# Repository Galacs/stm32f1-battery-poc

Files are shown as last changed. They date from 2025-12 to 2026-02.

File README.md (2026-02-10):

# STM32F1 Battery POC

STM32F1 based pcb to test 3s Li-ion cells protection with 3 phases brushless and steppers driver interfaces.

## IC List

- STM32F103C8T (Main MCU)
- QRE1113 (reflectance sensor)
- HT753-1 (3v3 LDO)
- LM78M (5v LDO)
- DRV8311 (BLDC driver)
- DRV8424 (Stepper driver)
- BQ77905 (3S battery protection)
- SN65HVD (CAN transceiver)

## Top preview




## Preview 3d render




## Pictures



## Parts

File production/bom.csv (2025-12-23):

Designator | Footprint | Quantity | Value | LCSC Part #
C1, C22, C23, C24, C31, C32, C34, C35, C41 | 0402 | 9 | 1u | C52923
C10, C15 | 0402 | 2 | 22n | C1532
C11, C12, C16, C18, C21, C26, C27, C28, C29, C3, C30, C33, C37, C38, C4, C40, C5, C6, C7 | 0402 | 19 | 0u1 | C307331
C13, C14 | 0603 | 2 | 20p | C1648
C17, C25, C36 | 0402 | 3 | 10n | C15195
C19 | 0603 | 1 | 0u47 | C1623
C2, C39, C43, C8, C9 | 0805 | 5 | 10u | C440198
C20, C42 | CP_Elec_6.3x7.7 | 2 | 100u | C165974
D1 | 0805 | 1 | YELLOW | C2296
D2 | 0603 | 1 | WHITE | C2290
D3 | 0805 | 1 | GREEN | C2297
D4 | 0603 | 1 | RED | C2286
D5 | D_SMB | 1 | D_TVS | C2925441
D6 | D_SOD-323 | 1 | 100 | C2128
D7 | D_SOD-123 | 1 | 16 | C19077429
FB1, FB2 | 0805 | 2 | 600Ω@100M | C1015
Q1, Q2 | Vishay_PowerPAK_1212-8_Single | 2 | Q_NMOS | C111309
R1, R32, R33, R6 | 0402 | 4 | 5k1 | C25905
R10, R11, R12 | 0603 | 3 | 47 | C23182
R13, R21 | 0603 | 2 | 330k | C23137
R14, R25, R28 | 0402 | 3 | 100 | C25076
R15, R16, R17, R18, R2, R29, R31 | 0402 | 7 | 10k | C25744
R19 | 0603 | 1 | 560 | C23204
R20, R22, R23, R24, R26 | 0402 | 5 | 1k | C11702
R27 | 1206 | 1 | 10m/1W | C105362
R3, R4, R5 | 0603 | 3 | 6k8 | C23212
R30, R35 | 0402 | 2 | 1M | C26083
R34 | 0603 | 1 | 3M | C23156
R36 | 0603 | 1 | 470k | C23178
R37, R38, R39 | 0402 | 3 | 47k | C25792
R7, R9 | 0603 | 2 | 20k | C4184
R8 | 1206 | 1 | 120 | C17909
SW1, SW2, SW3 | SW_SPST_TS-1088-xR020 | 3 | SW_Push | C720477
U1 | TO-252-2 | 1 | LM78M05 | C5145267
U10 | Texas_RRW0024A_WQFN-24-1EP_2x2mm_P0.4mmThermalVias | 1 | DRV8311H | C5218862
U2 | SOT-89-3 | 1 | HT753-1 | C14289
U3 | SOIC-8_3.9x4.9mm_P1.27mm | 1 | SN65HVD230 | C12084
U4, U5, U6 | OnSemi_CASE100CY | 3 | QRE1113GR | C232862
U7 | Texas_RGE0024B_VQFN-24-1EP_4x4mm_P0.5mm_EP2.5x2.5mm_ThermalVias | 1 | DRV8424RGER | C1518725
U8 | LQFP-48_7x7mm_P0.5mm | 1 | STM32F103C8Tx | C8734
U9 | TSSOP-20_4.4x6.5mm_P0.65mm | 1 | BQ77905 | C2866527
Y1 | Crystal_SMD_5032-2Pin_5.0x3.2mm | 1 | 8M | C115962

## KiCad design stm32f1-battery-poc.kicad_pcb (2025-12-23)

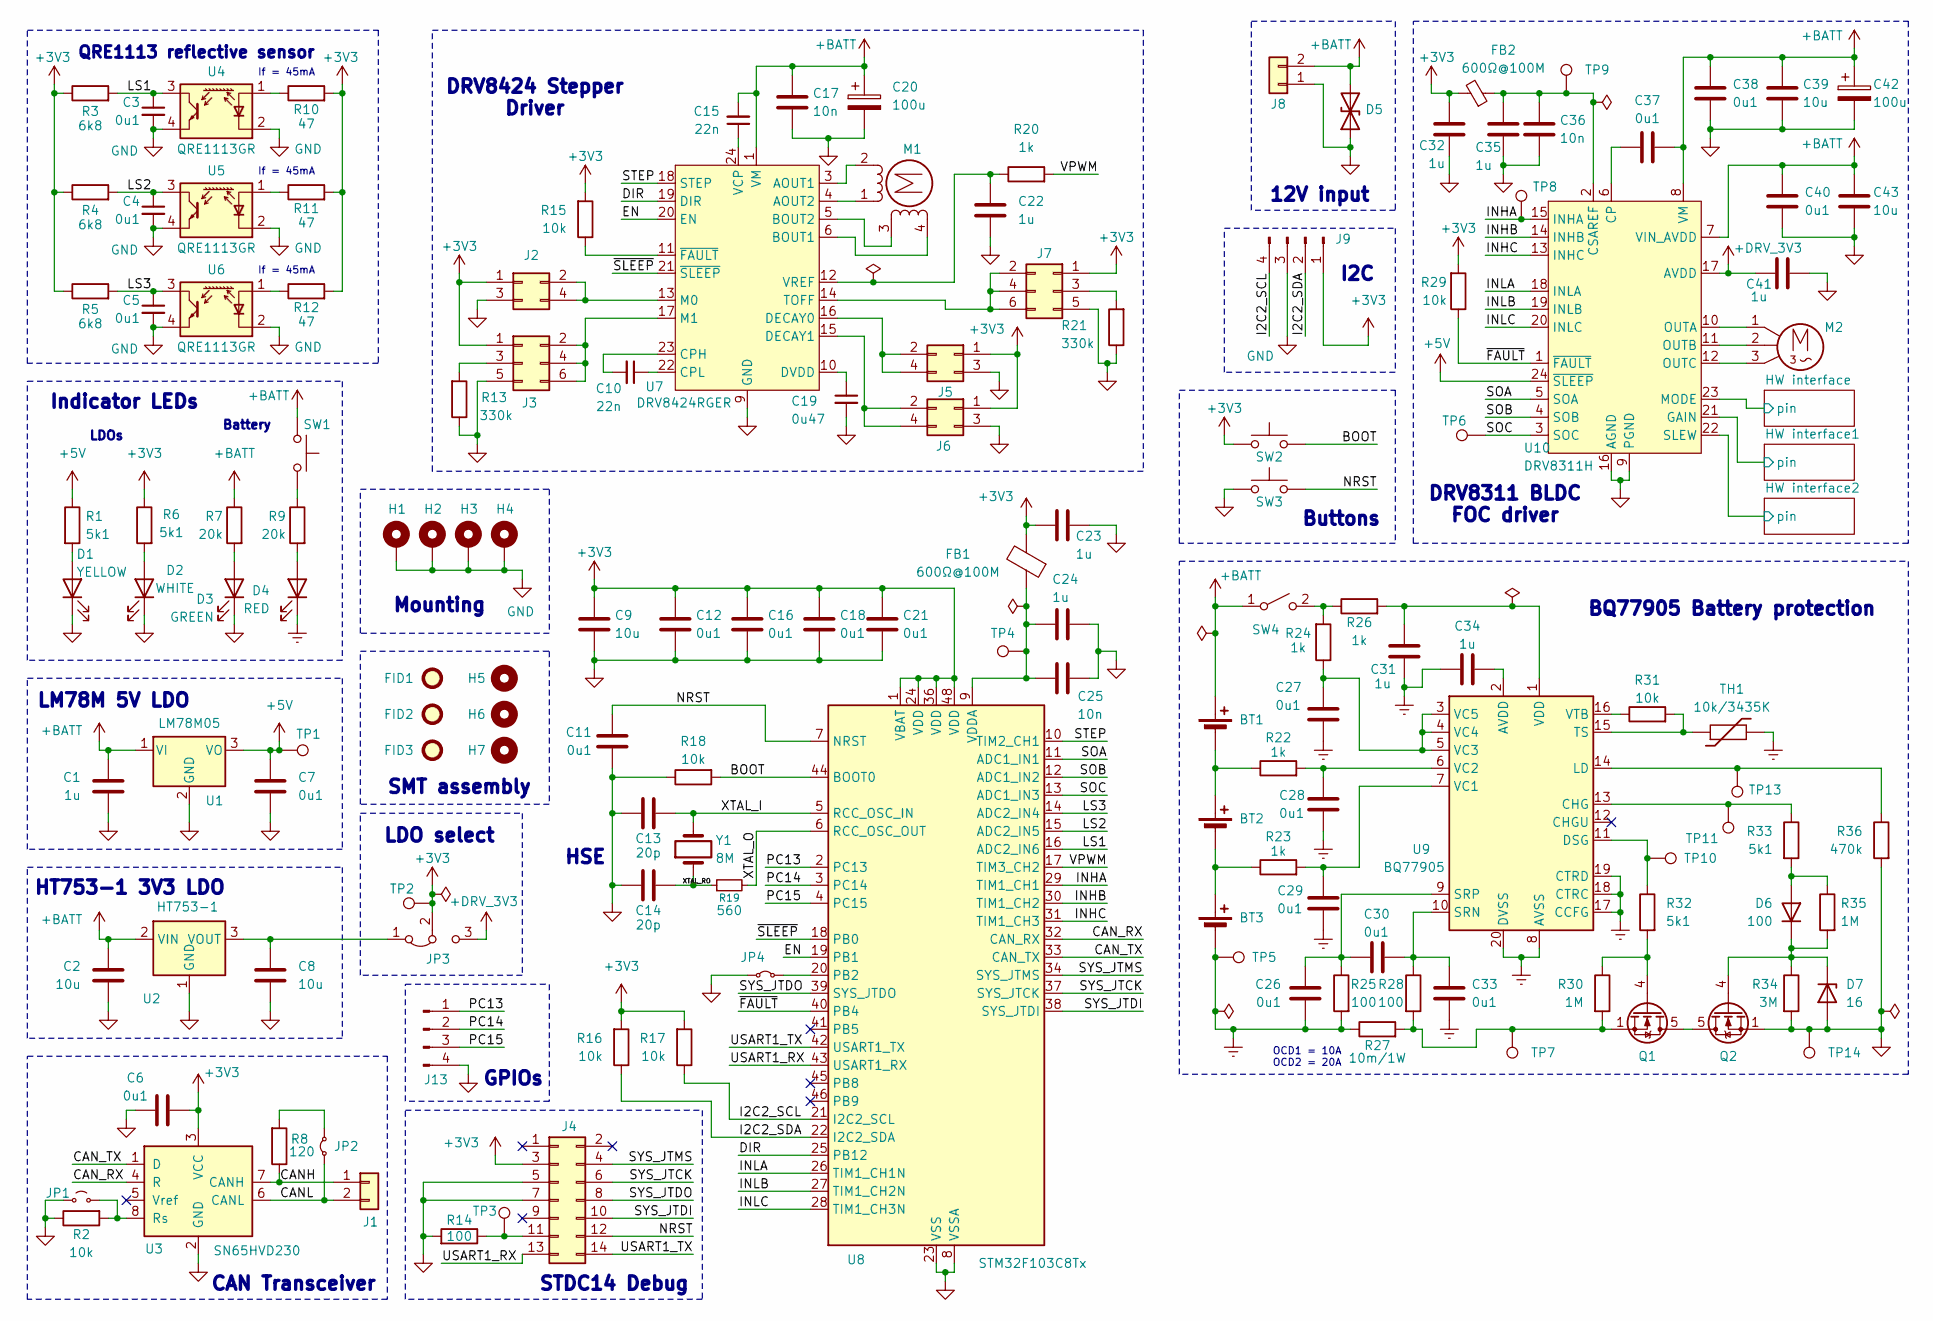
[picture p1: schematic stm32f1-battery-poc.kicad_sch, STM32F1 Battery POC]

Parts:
BT1, BT2, BT3: Battery_Cell; BatteryHolder_MYOUNG_BH-18650-B1BA002
C1, C22, C23, C24, C31, C32, C34, C35, C41: 1u; C_0402_1005Metric; Manufacturer Part Number CL05A105KA5NQNC; JLCPCB Part # C52923
C2, C8, C9, C39, C43: 10u; C_0805_2012Metric; Manufacturer Part Number GRM21BR61H106KE43L; JLCPCB Part # C440198
C3, C4, C5, C6, C7, C11, C12, C16, C18, C21, C26, C27, C28, C29, C30, C33, C37, C38, C40: 0u1; C_0402_1005Metric; Manufacturer Part Number CL05B104KB54PNC; JLCPCB Part # C307331
C10, C15: 22n; C_0402_1005Metric; Manufacturer Part Number 0402B223K500NT; JLCPCB Part # C1532
C13, C14: 20p; C_0603_1608Metric; Manufacturer Part Number CL10C200JB8NNNC; JLCPCB Part # C1648
C17, C25, C36: 10n; C_0402_1005Metric; Manufacturer Part Number CL05B103KB5NNNC; JLCPCB Part # C15195
C19: 0u47; C_0603_1608Metric; Manufacturer Part Number CL10B474KA8NNNC; JLCPCB Part # C1623
C20, C42: 100u; CP_Elec_6.3x7.7; Manufacturer Part Number EEEFTH101XAP; JLCPCB Part # C165974
D1: YELLOW; LED_0805_2012Metric; Manufacturer Part Number KT-0805Y; JLCPCB Part # C2296
D2: WHITE; LED_0603_1608Metric; Manufacturer Part Number KT-0603W; JLCPCB Part # C2290
D3: GREEN; LED_0805_2012Metric; Manufacturer Part Number KT-0805G; JLCPCB Part # C2297
D4: RED; LED_0603_1608Metric; Manufacturer Part Number KT-0603R; JLCPCB Part # C2286
D5: D_TVS; D_SMB; Manufacturer Part Number SMBJ30CA; JLCPCB Part # C2925441
D6: 100; D_SOD-323; Manufacturer Part Number 1N4148WS; JLCPCB Part # C2128
D7: 16; D_SOD-123; Manufacturer Part Number MMSZ5246B; JLCPCB Part # C19077429
FB1, FB2: 600Ω@100M; L_0805_2012Metric; Manufacturer Part Number GZ2012D101TF; JLCPCB Part # C1015
FID1, FID2, FID3: Fiducial; Fiducial_1mm_Mask2mm
H1, H2, H3, H4: MountingHole_Pad; MountingHole_2.2mm_M2_Pad_Via
H5, H6, H7: MountingHole; ToolingHole_1.152mm
J1: Conn_01x02; PinHeader_1x02_P2.54mm_Vertical
J2, J5, J6: Conn_02x02_Odd_Even; PinHeader_2x02_P1.27mm_Vertical_SMD
J3, J7: Conn_02x03_Odd_Even; PinHeader_2x03_P1.27mm_Vertical_SMD
J4: Conn_02x07_Odd_Even; PinHeader_2x07_P1.27mm_Vertical
J8: Conn_01x02; TerminalBlock_Phoenix_MKDS-1,5-2-5.08_1x02_P5.08mm_Horizont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
J9, J13: Conn_01x04_Pin; PinHeader_1x04_P2.54mm_Vertical
JP1: Jumper_2_Small_Open; PinHeader_2x01_P1.27mm_Vertical_SMD
JP2, JP4: Jumper_2_Small_Bridged; PinHeader_2x01_P1.27mm_Vertical_SMD
JP3: Jumper_3_Bridged12; PinHeader_1x03_P1.27mm_Vertical_SMD_Pin1Left
M1: Stepper_Motor_bipolar; JST_XH_S6B-XH-A_Stepper_1x06_P2.50mm_Horizontal
M2: Motor_3_Phases; PinHeader_1x03_P2.54mm_Vertical
Q1, Q2: Q_NMOS; Vishay_PowerPAK_1212-8_Single; Manufacturer Part Number SIS412DN-T1-GE3; JLCPCB Part # C111309
R1, R6, R32, R33: 5k1; R_0402_1005Metric; Manufacturer Part Number 0402WGF5101TCE; JLCPCB Part # C25905
R2, R15, R16, R17, R18, R29, R31: 10k; R_0402_1005Metric; Manufacturer Part Number 0402WGF1002TCE; JLCPCB Part # C25744
R3, R4, R5: 6k8; R_0603_1608Metric; Manufacturer Part Number 0603WAF6801T5E; JLCPCB Part # C23212
R7, R9: 20k; R_0603_1608Metric; Manufacturer Part Number 0603WAF2002T5E; JLCPCB Part # C4184
R8: 120; R_1206_3216Metric; Manufacturer Part Number 1206W4F1200T5E; JLCPCB Part # C17909
R10, R11, R12: 47; R_0603_1608Metric; Manufacturer Part Number 0603WAF470JT5E; JLCPCB Part # C23182
R13, R21: 330k; R_0603_1608Metric; Manufacturer Part Number 0603WAF3303T5E; JLCPCB Part # C23137
R14, R25, R28: 100; R_0402_1005Metric; Manufacturer Part Number 0402WGF1000TCE; JLCPCB Part # C25076
R19: 560; R_0603_1608Metric; Manufacturer Part Number 0603WAF5600T5E; JLCPCB Part # C23204
R20, R22, R23, R24, R26: 1k; R_0402_1005Metric; Manufacturer Part Number 0402WGF1001TCE; JLCPCB Part # C11702
R27: 10m/1W; R_1206_3216Metric; Manufacturer Part Number FMF06FTHR010-LH; JLCPCB Part # C105362
R30, R35: 1M; R_0402_1005Metric; Manufacturer Part Number 0402WGF1004TCE; JLCPCB Part # C26083
R34: 3M; R_0603_1608Metric; Manufacturer Part Number 0603WAF3004T5E; JLCPCB Part # C23156
R36: 470k; R_0603_1608Metric; Manufacturer Part Number 0603WAF4703T5E; JLCPCB Part # C23178
SW1, SW2, SW3: SW_Push; SW_SPST_TS-1088-xR020; Manufacturer Part Number TS-1088-AR02016; JLCPCB Part # C720477
SW4: SW_SPST; PinHeader_1x02_P2.54mm_Vertical
TH1: 10k/3435K; PinSocket_1x02_P2.54mm_Vertical
TP1, TP2, TP3, TP4, TP5, TP6, TP7, TP8, TP9, TP10, TP11, TP13, TP14: TestPoint; TestPoint_Pad_D2.0mm
U1: LM78M05; TO-252-2; Manufacturer Part Number LM78M05ACKTPRG; JLCPCB Part # C5145267
U2: HT753-1; SOT-89-3; Manufacturer Part Number HT7533-1; JLCPCB Part # C14289
U3: SN65HVD230; SOIC-8_3.9x4.9mm_P1.27mm; Manufacturer Part Number SN65HVD230DR; JLCPCB Part # C12084
U4, U5, U6: QRE1113GR; OnSemi_CASE100CY; Manufacturer Part Number QRE1113GR; JLCPCB Part # C232862
U7: DRV8424RGER; Texas_RGE0024B_VQFN-24-1EP_4x4mm_P0.5mm_EP2.5x2.5mm_Thermal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; Manufacturer Part Number DRV8424RGER; JLCPCB Part # C1518725
U8: STM32F103C8Tx; LQFP-48_7x7mm_P0.5mm; Manufacturer Part Number STM32F103C8T6; JLCPCB Part # C8734
U9: BQ77905; TSSOP-20_4.4x6.5mm_P0.65mm; Manufacturer Part Number BQ7790509PWR; JLCPCB Part # C2866527
U10: DRV8311H; Texas_RRW0024A_WQFN-24-1EP_2x2mm_P0.4mmThermalVias; Manufacturer Part Number DRV8311HRRWR; JLCPCB Part # C5218862
Y1: 8M; Crystal_SMD_5032-2Pin_5.0x3.2mm; Manufacturer Part Number X50328MSB2GI; JLCPCB Part # C115962

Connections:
+3V3: C6.1, C9.1, C12.1, C16.1, C18.1, C21.1, C23.1, C32.1, FB1.2, FB2.2, J2.1, J3.1, J4.3, J5.1, J6.1, J7.1, J9.1, JP3.2 (C), R3.1, R4.1, R5.1, R6.1, R10.2, R11.2, R12.2, R15.2, R16.2, R17.2, R29.2, SW2.1, TP2.1, U3.3 (VCC), U8.1 (VBAT), U8.24 (VDD), U8.36 (VDD), U8.48 (VDD); also elsewhere on the board
+5V: C7.1, R1.1, TP1.1, U1.3 (VO), U10.24 (~SLEEP)
+BATT: BT1.1 (+), C1.1, C2.1, C15.2, C17.1, C20.1, C37.2, C38.2, C39.2, C40.2, C42.1, C43.2, D5.2 (A2), J8.2, R7.1, SW1.2, SW4.1 (A), U1.1 (VI), U2.2 (VIN), U7.1 (VM), U7.8 (VM), U10.7 (VIN_AVDD), U10.8 (VM)
+DRV_3V3: C41.1, JP3.3 (B), U10.17 (AVDD)
/BOOT: R18.2, SW2.2, U8.44 (BOOT0)
/CANH: J1.1, R8.1, U3.7 (CANH)
/CANL: J1.2, JP2.1 (A), U3.6 (CANL)
/CAN_RX: U3.4 (R), U8.32 (CAN_RX)
/CAN_TX: U3.1 (D), U8.33 (CAN_TX)
/DIR: U7.19 (DIR), U8.25 (PB12)
/EN: U7.20 (EN), U8.19 (PB1)
/HW interface1/pin: U10.21 (GAIN); also elsewhere on the board
/HW interface2/pin: U10.22 (SLEW); also elsewhere on the board
/HW interface/pin: U10.23 (MODE); also elsewhere on the board
/I2C2_SCL: J9.4, R17.1, U8.21 (I2C2_SCL)
/I2C2_SDA: J9.2, R16.1, U8.22 (I2C2_SDA)
/INHA: TP8.1, U8.29 (TIM1_CH1), U10.15 (INHA)
/INHB: U8.30 (TIM1_CH2), U10.14 (INHB)
/INHC: U8.31 (TIM1_CH3), U10.13 (INHC)
/INLA: U8.26 (TIM1_CH1N), U10.18 (INLA)
/INLB: U8.27 (TIM1_CH2N), U10.19 (INLB)
/INLC: U8.28 (TIM1_CH3N), U10.20 (INLC)
/LS1: C3.1, R3.2, U4.3, U8.16 (ADC2_IN6)
/LS2: C4.1, R4.2, U5.3, U8.15 (ADC2_IN5)
/LS3: C5.1, R5.2, U6.3, U8.14 (ADC2_IN4)
/NRST: C11.1, J4.12, SW3.2, U8.7 (NRST)
/PC13: J13.1, U8.2 (PC13)
/PC14: J13.2, U8.3 (PC14)
/PC15: J13.3, U8.4 (PC15)
/SOA: U8.11 (ADC1_IN1), U10.5 (SOA)
/SOB: U8.12 (ADC1_IN2), U10.4 (SOB)
/SOC: TP6.1, U8.13 (ADC1_IN3), U10.3 (SOC)
/STEP: U7.18 (STEP), U8.10 (TIM2_CH1)
/SYS_JTCK: J4.6, U8.37 (SYS_JTCK)
/SYS_JTDI: J4.10, U8.38 (SYS_JTDI)
/SYS_JTDO: J4.8, U8.39 (SYS_JTDO)
/SYS_JTMS: J4.4, U8.34 (SYS_JTMS)
/USART1_RX: J4.13, U8.43 (USART1_RX)
/USART1_TX: J4.14, U8.42 (USART1_TX)
/VPWM: R20.2, U8.17 (TIM3_CH2)
/XTAL_I: C13.1, U8.5 (RCC_OSC_IN), Y1.2
/XTAL_O: R19.2, U8.6 (RCC_OSC_OUT)
/XTAL_RO: C14.1, R19.1, Y1.1
/~FAULT: R29.1, U8.40 (PB4), U10.1 (~FAULT)
/~SLEEP: U7.21 (~SLEEP), U8.18 (PB0)
BGND: BT3.2 (-), C26.2, C27.2, C28.2, C29.2, C31.1, C33.2, C34.2, D4.1 (K), R25.2, R27.1, TH1.2, TP5.1, U9.8 (AVSS), U9.17 (CCFG), U9.18 (CTRC), U9.19 (CTRD), U9.20 (DVSS)
GND: C1.2, C2.2, C3.2, C4.2, C5.2, C6.2, C7.2, C8.2, C9.2, C11.2, C12.2, C13.2, C14.2, C16.2, C17.2, C18.2, C19.2, C20.2, C21.2, C22.2, C23.2, C24.2, C25.2, C32.2, C35.2, C36.2, C38.1, C39.1, C40.1, C41.2, C42.2, C43.1, D1.1 (K), D2.1 (K), D3.1 (K), D5.1 (A1), D7.2 (A), H1.1, H2.1, H3.1, H4.1, J2.3, J3.5, J4.5, J4.7, J5.3, J6.3, J7.5, J8.1, J9.3, J13.4, JP1.1 (A), JP4.1 (A), Q2.1 (S), Q2.2 (S), Q2.3 (S), R2.1, R13.1, R14.2, R18.1, R21.1, R34.2, R36.2, SW3.1, TP14.1, U1.2 (GND), U2.1 (GND), U3.2 (GND), U4.2 (K), U4.4, U5.2 (K), U5.4, U6.2 (K), U6.4, U7.2 (PGND), U7.7 (PGND), U7.9 (GND), U7.25 (GND), U8.8 (VSSA), U8.23 (VSS), U8.35 (VSS), U8.47 (VSS), U10.9 (PGND), U10.16 (AGND), U10.25 (EPAD); also elsewhere on the board
unnamed: BT1.2 (-), BT2.1 (+), R22.1
unnamed: BT2.2 (-), BT3.1 (+), R23.1
unnamed: D1.2 (A), R1.2
unnamed: D2.2 (A), R6.2
unnamed: D3.2 (A), R7.2
unnamed: D4.2 (A), R9.2
unnamed: D6.2 (A), R33.2, R35.1
unnamed: D6.1 (K), D7.1 (K), Q2.4 (G), R34.1, R35.2
unnamed: J2.2, J2.4, U7.13 (M0)
unnamed: J3.2, J3.4, J3.6, U7.17 (M1)
unnamed: J3.3, R13.2
unnamed: J4.11, R14.1, TP3.1
unnamed: J5.2, J5.4, U7.16 (DECAY0)
unnamed: J6.2, J6.4, U7.15 (DECAY1)
unnamed: J7.2, J7.4, J7.6, U7.14 (TOFF)
unnamed: J7.3, R21.2
unnamed: JP1.2 (B), R2.2, U3.8 (Rs)
unnamed: JP2.2 (B), R8.2
unnamed: C8.1, JP3.1 (A), U2.3 (VOUT)
unnamed: JP4.2 (B), U8.20 (PB2)
unnamed: M1.2 (-), U7.3 (AOUT1)
unnamed: Q1.5 (D), Q2.5 (D)
unnamed: Q1.4 (G), R30.1, R32.2
unnamed: Q1.1 (S), Q1.2 (S), Q1.3 (S), R27.2, R28.2, R30.2, TP7.1
unnamed: R9.1, SW1.1
unnamed: R24.2, R26.1, SW4.2 (B)
unnamed: R10.1, U4.1 (A)
unnamed: R11.1, U5.1 (A)
unnamed: R12.1, U6.1 (A)
unnamed: M1.1, U7.4 (AOUT2)
unnamed: M1.4, U7.6 (BOUT1)
unnamed: M1.3, U7.5 (BOUT2)
unnamed: C10.2, U7.23 (CPH)
unnamed: C10.1, U7.22 (CPL)
unnamed: C19.1, U7.10 (DVDD)
unnamed: C15.1, U7.24 (VCP)
unnamed: C22.1, R20.1, U7.12 (VREF)
unnamed: R15.1, U7.11 (~FAULT)
unnamed: C24.1, C25.1, FB1.1, TP4.1, U8.9 (VDDA)
unnamed: C34.1, U9.2 (AVDD)
unnamed: R33.1, TP11.1, U9.13 (CHG)
unnamed: R32.1, TP10.1, U9.11 (DSG)
unnamed: R36.1, TP13.1, U9.14 (LD)
unnamed: C30.1, C33.1, R28.1, U9.10 (SRN)
unnamed: C26.1, C30.2, R25.1, U9.9 (SRP)
unnamed: R31.2, TH1.1, U9.15 (TS)
unnamed: C29.1, R23.2, U9.7 (VC1)
unnamed: C28.1, R22.2, U9.6 (VC2)
unnamed: C27.1, R24.1, U9.3 (VC5), U9.4 (VC4), U9.5 (VC3)
unnamed: C31.2, R26.2, U9.1 (VDD)
unnamed: R31.1, U9.16 (VTB)
unnamed: C37.1, U10.6 (CP)
unnamed: C35.1, C36.1, FB2.1, TP9.1, U10.2 (CSAREF)
unnamed: M2.1, U10.10 (OUTA)
unnamed: M2.2, U10.11 (OUTB)
unnamed: M2.3, U10.12 (OUTC)

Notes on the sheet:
Buttons
If = 45mA
LDOs
BQ77905 Battery protection
QRE1113 reflective sensor
SMT assembly
DRV8424 Stepper Driver
LDO select
LM78M 5V LDO
HSE
DRV8311 BLDC FOC driver
GPIOs
OCD1 = 10A OCD2 = 20A
STDC14 Debug
12V input
Mounting
Battery
I2C
HT753-1 3V3 LDO
Indicator LEDs
CAN Transceiver

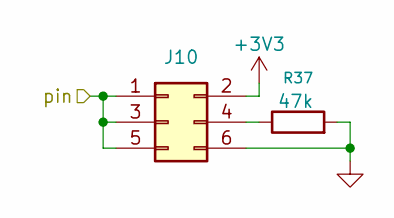
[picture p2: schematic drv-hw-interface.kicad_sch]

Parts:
J10: Conn_02x03_Odd_Even; PinHeader_2x03_P1.27mm_Vertical_SMD
R37: 47k; R_0402_1005Metric; Manufacturer Part Number 0402WGF4702TCE; JLCPCB Part # C25792

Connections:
+3V3: J10.2; also elsewhere on the board
/HW interface/pin: J10.1, J10.3, J10.5; also elsewhere on the board
GND: J10.6, R37.2; also elsewhere on the board
unnamed: J10.4, R37.1

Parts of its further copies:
J11, J12: Conn_02x03_Odd_Even; PinHeader_2x03_P1.27mm_Vertical_SMD
R38, R39: 47k; R_0402_1005Metric; Manufacturer Part Number 0402WGF4702TCE; JLCPCB Part # C25792

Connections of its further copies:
+3V3: J11.2, J12.2; also elsewhere on the board
/HW interface1/pin: J11.1, J11.3, J11.5; also elsewhere on the board
/HW interface2/pin: J12.1, J12.3, J12.5; also elsewhere on the board
GND: J11.6, J12.6, R38.2, R39.2; also elsewhere on the board
unnamed: J11.4, R38.1
unnamed: J12.4, R39.1

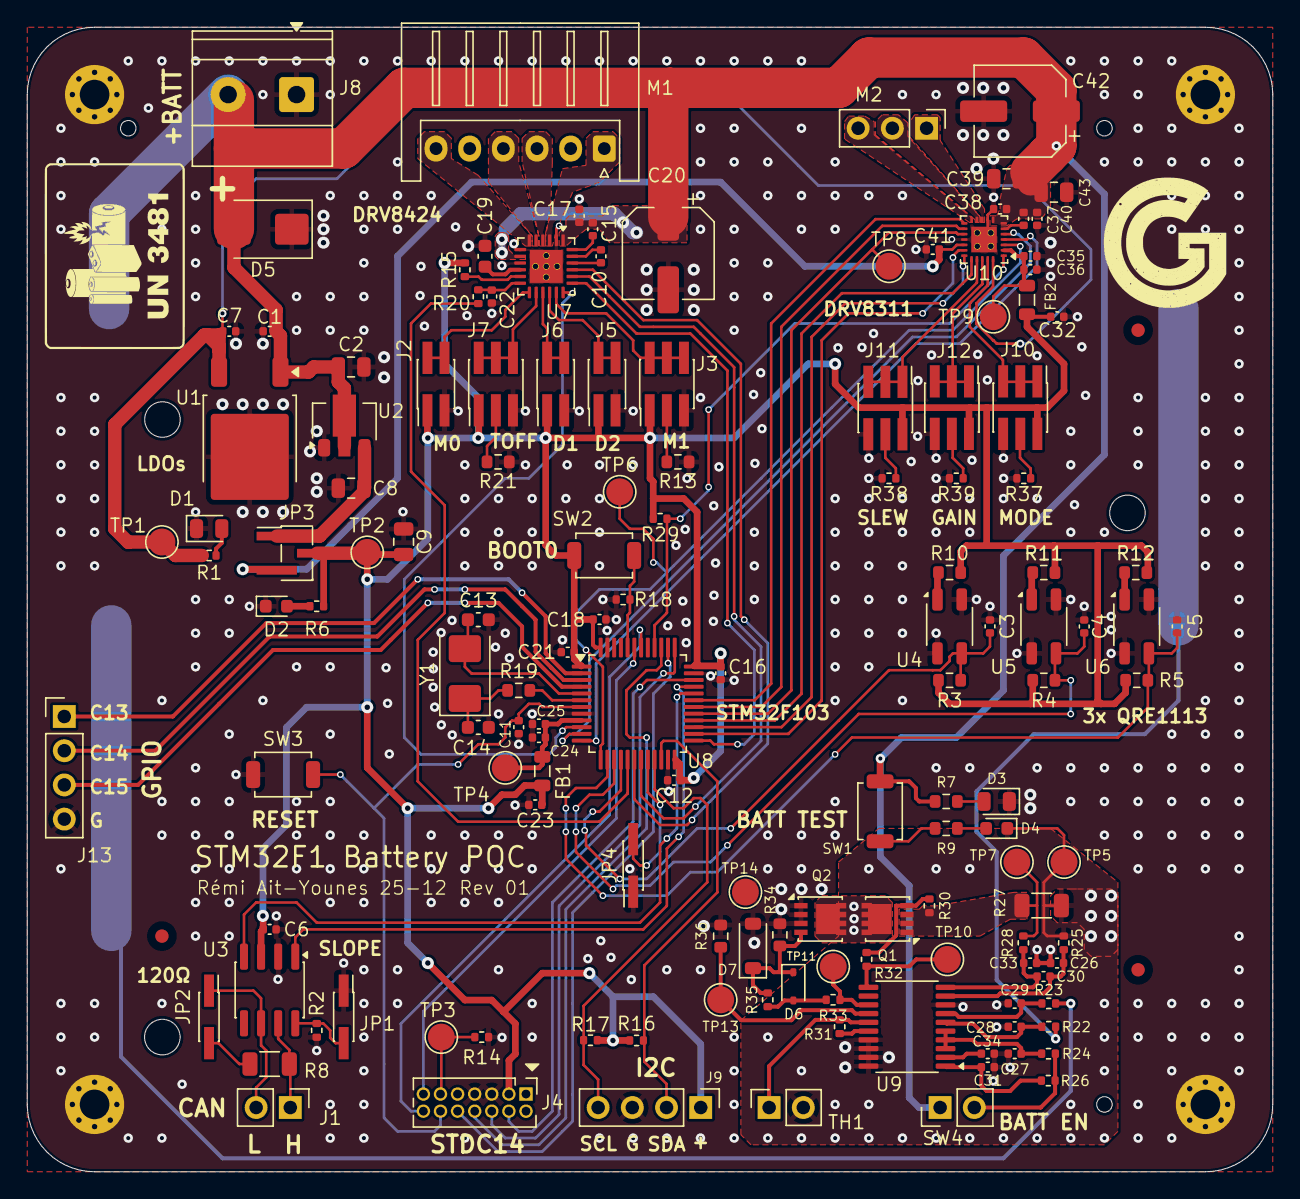
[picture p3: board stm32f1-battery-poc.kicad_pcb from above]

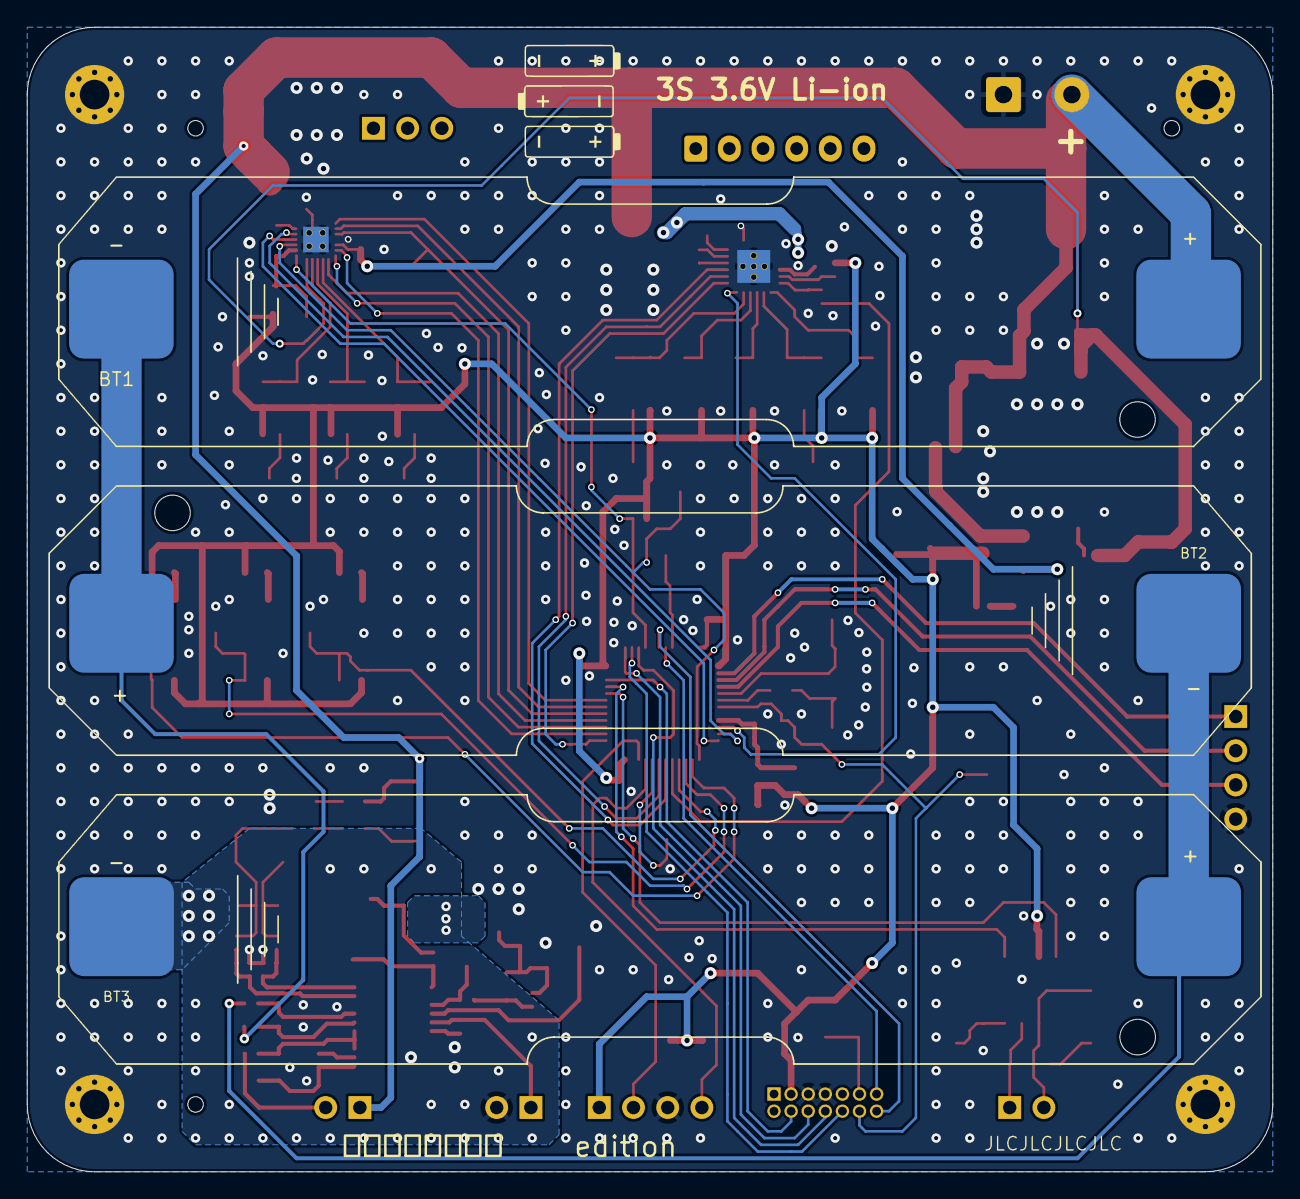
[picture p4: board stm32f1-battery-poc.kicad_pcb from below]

Board: 4 copper layers, 92.5 x 85.0 mm, 154 parts (3 on the bottom side), 106 nets.

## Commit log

2025-12-06 schem: add STM32F103C8T6 symbol
    [stm32f1-battery-poc.kicad_sch]
2025-12-06 schem: add decoupling capacitors
    [stm32f1-battery-poc.kicad_sch]
2025-12-06 schem: add BOOT0 pulldown
    [stm32f1-battery-poc.kicad_sch]
2025-12-06 pcb: add BOOT and RST buttons
    [stm32f1-battery-poc.kicad_sch]
2025-12-06 schem: add 8Mhz HSE
    [stm32f1-battery-poc.kicad_sch]
2025-12-07 schem: add STDC14 Debug port
    [stm32f1-battery-poc.kicad_sch]
2025-12-07 schem: add SN65HVD230 CAN transceiver
    [stm32f1-battery-poc.kicad_sch]
2025-12-07 schem: add BQ77905 Battery protection
    [stm32f1-battery-poc.kicad_sch]
2025-12-07 schem: add battery cells to BQ77905
    [stm32f1-battery-poc.kicad_sch]
2025-12-07 schem: add FB to VDDA
    [stm32f1-battery-poc.kicad_sch]
2025-12-08 schem: add power indicator LEDs
    [stm32f1-battery-poc.kicad_sch]
2025-12-08 schem: add BQ77905 enable switch
    [stm32f1-battery-poc.kicad_sch]
2025-12-08 schem: add BQ77905 rsense filter
    [stm32f1-battery-poc.kicad_sch]
2025-12-08 schem: add LM78M 5V LDO
    [stm32f1-battery-poc.kicad_sch]
2025-12-08 schem: add HT753-1 3V3 LDO
    [stm32f1-battery-poc.kicad_sch]
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2025-12-08 schem: add 3V3 ldo select
    [stm32f1-battery-poc.kicad_sch]
2025-12-08 schem: add 12V power input
    [stm32f1-battery-poc.kicad_sch]
2025-12-08 schem: add DRV8311 bldc driver
    [stm32f1-battery-poc.kicad_sch]
2025-12-09 schem: add DRV8311 hardware pin config jumpers
    [drv-hw-interface.kicad_sch, stm32f1-battery-poc.kicad_sch]
2025-12-09 schem: import QRE1113 reflective sensor from motor-power-poc
    [stm32f1-battery-poc.kicad_sch]
2025-12-09 schem: add BQ77905 shunt resistor value
    [stm32f1-battery-poc.kicad_sch]
2025-12-09 schem: clean up LDO select
    [stm32f1-battery-poc.kicad_sch]
2025-12-09 schem: add DRV8311 missing power inputs
    [stm32f1-battery-poc.kicad_sch]
2025-12-10 schem: add DRV8311 nSLEEP pullup
    [stm32f1-battery-poc.kicad_sch]
2025-12-10 schem: connect DRV8311 to MCU
    [stm32f1-battery-poc.kicad_sch]
2025-12-11 schem: connect QRE1113 to MCU
    [stm32f1-battery-poc.kicad_sch]
2025-12-11 schem: add HSE external components values
    [stm32f1-battery-poc.kicad_sch]
2025-12-12 schem: add NCs to MCU
    [stm32f1-battery-poc.kicad_sch]
2025-12-12 schem: add test points
    [stm32f1-battery-poc.kicad_sch]
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2025-12-12 schem: add net classes
    [stm32f1-battery-poc.kicad_sch]
2025-12-12 schem: run and fix ERC
    [stm32f1-battery-poc.kicad_sch]
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2025-12-12 schem: regorganize to leave space for DRV8424RGER
    [drv-hw-interface.kicad_sch, stm32f1-battery-poc.kicad_sch]
2025-12-12 schem: add DRV8424RGER stepper driver
    [stm32f1-battery-poc.kicad_sch]
2025-12-12 schem: add DRV8424 mode setting jumpers
    [stm32f1-battery-poc.kicad_sch]
2025-12-20 schem: add I2C connector
    [stm32f1-battery-poc.kicad_sch]
2025-12-20 schema: connect DRV8424 vref pin
    [stm32f1-battery-poc.kicad_sch]
2025-12-21 schem: add footprints and ordering info to BOM
    [drv-hw-interface.kicad_sch, stm32f1-battery-poc.kicad_sch]
2025-12-21 schem: add missing DRV8424 MCU connections
    [stm32f1-battery-poc.kicad_sch]
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2025-12-21 schem: fix symbols orientations
    [stm32f1-battery-poc.kicad_sch]
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2025-12-21 pbb: import stackup and constraints
    [stm32f1-battery-poc.kicad_pcb]
2025-12-21 pcb: import footprints from schematic
    [stm32f1-battery-poc.kicad_pcb]
2025-12-21 pcb: add missing 3d models
    [stm32f1-battery-poc.kicad_pcb]
2025-12-21 pcb: initial rough layout
    [stm32f1-battery-poc.kicad_pcb]
2025-12-21 schem/pcb: add fiducials, mounting and tooling holes
    [stm32f1-battery-poc.kicad_pcb, stm32f1-battery-poc.kicad_sch]
2025-12-21 schem/pcb: change jumpers to smd
    [drv-hw-interface.kicad_sch, stm32f1-battery-poc.kicad_pcb, stm32f1-battery-poc.kicad_sch]
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2025-12-21 pcb: add holes layout
    [stm32f1-battery-poc.kicad_pcb]
2025-12-21 pcb: add board outline
    [stm32f1-battery-poc.kicad_pcb]
2025-12-21 pcb: refine connectors positions
    [stm32f1-battery-poc.kicad_pcb]
2025-12-21 pcb: add grid/drill origin
    [stm32f1-battery-poc.kicad_pcb]
2025-12-21 pcb: add gnd planes
    [stm32f1-battery-poc.kicad_pcb]
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2025-12-21 pcb: add gnd vias
    [stm32f1-battery-poc.kicad_pcb]
2025-12-21 schem: change I2C pins
    [stm32f1-battery-poc.kicad_pcb, stm32f1-battery-poc.kicad_sch]
2025-12-21 pcb: add CAN layout
    [stm32f1-battery-poc.kicad_pcb]
2025-12-21 pcb: add STDC14 debug port routing
    [stm32f1-battery-poc.kicad_pcb]
2025-12-21 pcb: add CAN routing
    [stm32f1-battery-poc.kicad_pcb]
2025-12-21 pcb: add DRV8311 routing
    [stm32f1-battery-poc.kicad_pcb]
2025-12-21 pcb: add BQ77905 routing
    [stm32f1-battery-poc.kicad_pcb, stm32f1-battery-poc.kicad_sch]
2025-12-21 pcb: add DRV8424 stepper driver routing
    [stm32f1-battery-poc.kicad_pcb, stm32f1-battery-poc.kicad_sch]
2025-12-21 pcb: add I2C connector routing
    [stm32f1-battery-poc.kicad_pcb]
2025-12-21 pcb: add power ldos routing
    [stm32f1-battery-poc.kicad_pcb]
2025-12-21 pcb: add 3v3 power routing
    [stm32f1-battery-poc.kicad_pcb]
2025-12-21 pcb: add QRE1113 routing
    [stm32f1-battery-poc.kicad_pcb, stm32f1-battery-poc.kicad_sch]
2025-12-21 pcb: add NRST routing
    [stm32f1-battery-poc.kicad_pcb]
2025-12-21 pcb: add 5V routnig
    [stm32f1-battery-poc.kicad_pcb]
2025-12-21 pcb: add missing connections
    [stm32f1-battery-poc.kicad_pcb]
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2025-12-21 pcb: run and fix DRC
    [stm32f1-battery-poc.kicad_pcb]
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2025-12-23 pcb(silkscreen): replace placeholder
    [stm32f1-battery-poc.kicad_pcb]
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
